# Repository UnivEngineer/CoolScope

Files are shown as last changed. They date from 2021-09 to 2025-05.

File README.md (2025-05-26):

# CoolScope
Telescope fan controller

CoolScope is a diy 2-channel fan controller based on Arduino Nano. It is used to cool down (thermostabilize) the 12 inch Meade LX200 telescope, but can be adapted to any other scope. It is assembled in a 3D printed case and mounted on the back on the scope. The device features 2 channels for 12V PWM fans, 4 temperature sensors DS18B20 (mounted on the scope's primary mirror, inside the scope's tube, inside device's case, and one external sensor connected via 3.5 mm jack), and 1602 LCD/OLED display to show stats and menu. The device is powered by 12V external power source, and draws up to 400 mA (depending on used fans).

The project consists of three parts:

Telescope_fans - Arduino sketch source code.
PCB - KiCad files of circuit schematics and PCB.
Case - SolidWorks and STL files of 3D model of the case.

The device can use any 80 mm 1602 LCD module with parallel interface (4 data lines). The best choice for astronomy accessory is a module with red symbols on a black background. Even better choice is a red Winstar 1602 OLED (WEH001602A), fully compatible electrically with LCD modules. OLED display performance is perfect at freezing temperatures, unlike STN LCD. The device supports both types of displays, there is a jumper on the PCB to tell the software which type of display module is connected.

The Arduino Nano can either be soldered to the main PCB through its PLS pins, or installed in a DIP socket, but you have to cut and solder pins directly to Nano, otherwise it may not fit under the display module.

The device has the circuit which protects it against wrong power polarity, and power voltage monitor, which can be used to control telescope's battery charge, and also used by software to auto-save settings to EEPROM memory on power loss.

----------------------------------------------------------------------------------

Short usage manual (v 1.5)

Device has 4 buttons: [menu], [<], [>], [ok].

Once powered up, you will see the info screen. It displays current temperatures reported by sensors, fans speed and duty, and power supply voltage. You may scroll through info screen modes by pressing [<] and [>] buttons. Legend:

- A - ambient temperature, i.e. sensor inside the device
- E - external temperature, i.e. external sensor connected via jack
- M - mirror temperature
- T - tube temperature (air inside the tube)
- [battery symbol] - power supply voltage
- [rotating fan symbol] - max of (front, rear) fans duty/RPM
- F - front fan duty/RPM
- R - rear fan duty/RPM

Pressing [menu] or [ok] button will bring up the settings. Press buttons [<] or [>] to scroll through options or increase/decrease values, [ok] to enter sub-level, [menu] to return back to upper level. The settings menu hierarchy is the following:

Settings
- Cooling
  - Fans enabled [values are "off", "on"]
  - Mode once cooled [values are "Keep delta T", "Keep blowing", "Keep drawing", "Stop"]
  - Target delta T [values are 0.05, 0.1, 0.2 ... 3.0 °C]
  - Cooling speed [values are 5, 10, 15 ... 100 %]
  - Keeping speed [values are 5, 10, 15 ... 100 %]
  - Pos. pressure [values are 0, 5, 10, 15 ... 100 %]
- Sensors
  - Target delta T pair [values are "Mirror and Ambient", "Mirror and External", "Mirror and Tube"]
  - Assign sensors [scroll through list of detected DS18B20 addresses and press [menu] to assign]
    - Mirror
    - Tube
    - Ambient
    - External
- Display
  - Brightness [values are 0, 1, ... 10]
  - Contrast [LCD only; values are 1, ... 10]
  - Timeout [values are "Disabled", 5, 10, 15, ..., 120 seconds]
  - Test [all pixels of display are filled until [menu] is pressed]
- Information
  - Uptime [uptime in days hours:minutes:seconds]
  - Fan stuck alarm [values are "off", "on"]
  - Low battery alarm [values are "off", "on"]
  - Battery alarm voltage [values are 8.0, 8.1, ... 12.0 volts]
  - Power voltage [current power supply voltage]
  - About

Pressing and holding the menu button, while on the info screen, will disable/enable cooling (the message "Fans enabled"/"Fans disabled" is displayed for a few seconds). This is a quicker way to stop fans than accessing "Cooling->Fans enabled" menu.

Depending on "Display->Timeout" settings, the display may turn off after a while (if LCD is used, only back-light will turn off). To turn on it back, simply press any button.

The device will run fans at "Cooling->Cooling speed" duty until specified delta T is reached. After that, it will either stop fans or keep them spinning at "Cooling->Keeping speed". Typically, you need the primary mirror of your scope to be in thermal equilibrium with outside air, so the "Target delta T pair" must be set to "Mirror and External", and external DS18B20 sensor plugged into the 3.5 mm jack. The "Ambient" sensor is mounted inside the device, thus may report higher temperatures because of observer breathing. For a balcony observations, the "Mirror and Tube" pair may give better results, because air at balcony is warmer than the outside air anyway.

To protect interior of the scope from the dust, intake fans must be covered with dust filters (HEPA is the best solution). Also it is important to keep the pressure inside the tube a bit higher than the atmosphere, otherwise unfiltered air with dust particles may be sucked in from holes and slits. Thus intake fans must spin somewhat faster that exhaust fans. The "Cooling->Pos. pressure" menu sets the percentage of the exhaust fans speed in relation to intake fans speed. Typical value is 30-50%. You can find it experimentally using a plastic bag capping the eyepiece slot of your scope: the bag must inflate.

V 1.2 - added auto switch to external sensor, then plugged in; added CRC check of data read from sensors.
V 1.3 - added support for graphical Winstar OLED (100x16 pixels) as a define, switch OLED/LCD is not supported in this case.
V 1.4 - fixed bug with "About" menu not working properly.
V 1.5 - added exhaust fans duty adjust.

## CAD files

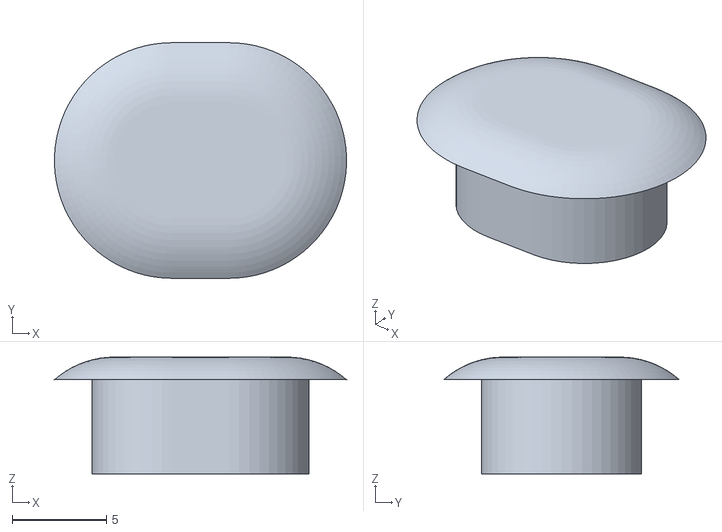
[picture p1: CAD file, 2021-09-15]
Сase/Dummy^Assembly.STL
15.5 x 12.5 x 6.20

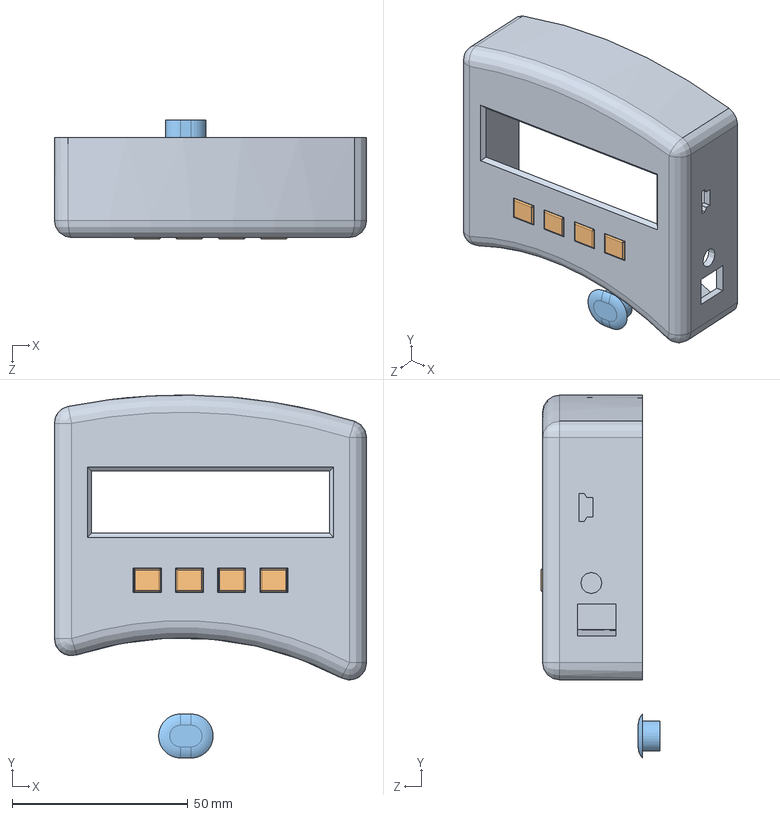
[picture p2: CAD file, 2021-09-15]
Сase/Assembly.SLDASM
88.8 x 103.2 x 33.8 mm
Case
Button1 x 4
Dummy^Assembly

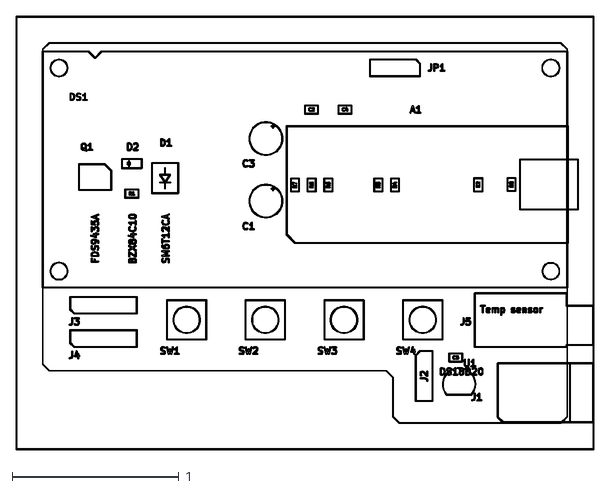
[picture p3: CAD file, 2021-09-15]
Сase/Telescope_fans-F_Fab.dxf
3.47 x 2.60

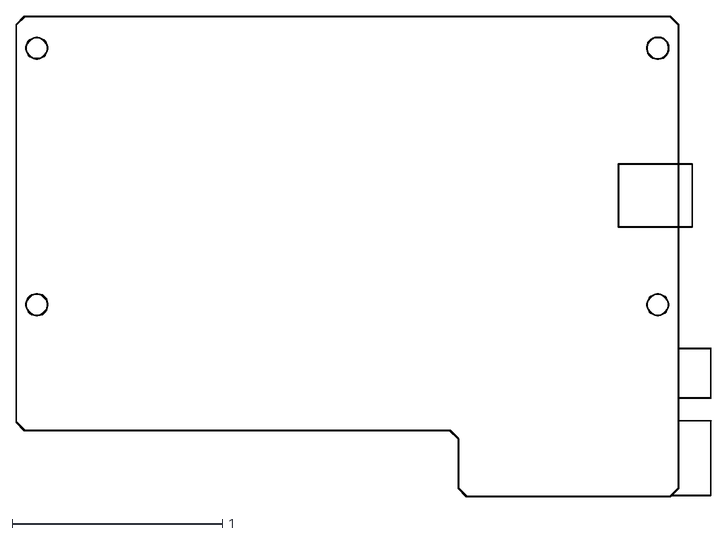
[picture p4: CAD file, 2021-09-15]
Сase/Telescope_fans-Edge_Cuts.dxf
3.30 x 2.29

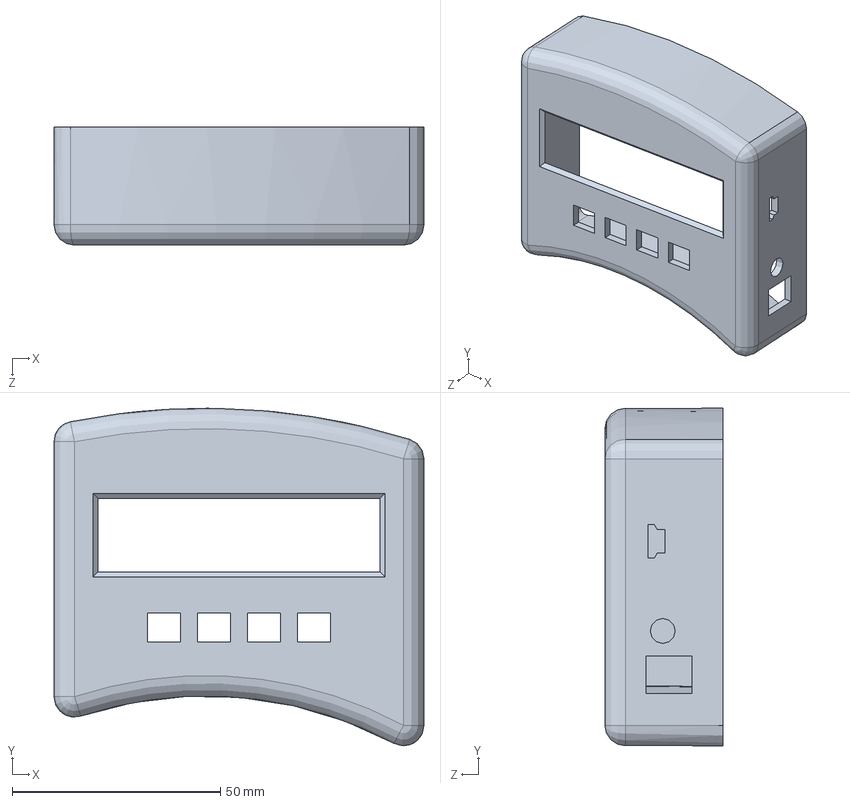
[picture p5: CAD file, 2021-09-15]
Сase/Case.SLDPRT
88.8 x 81.0 x 28.4 mm

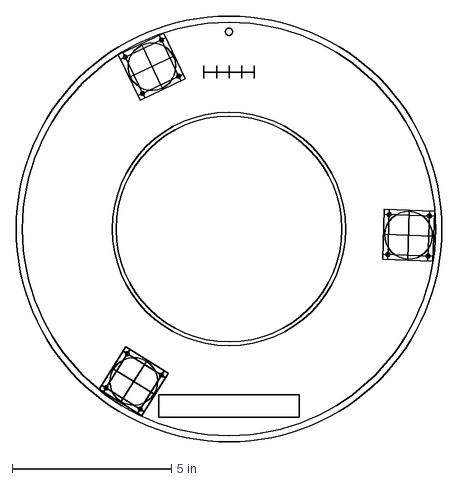
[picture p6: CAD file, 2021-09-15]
Сase/scope_back.dxf
13.4 x 13.4 in

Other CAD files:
Сase/Cover.SLDPRT
Сase/Button1.SLDPRT
Сase/Button1.STL
Сase/Case.STL
Сase/Cover.STL
Сase/Telescope_fans-B_Mask.dxf
Сase/Telescope_fans-F_SilkS.dxf

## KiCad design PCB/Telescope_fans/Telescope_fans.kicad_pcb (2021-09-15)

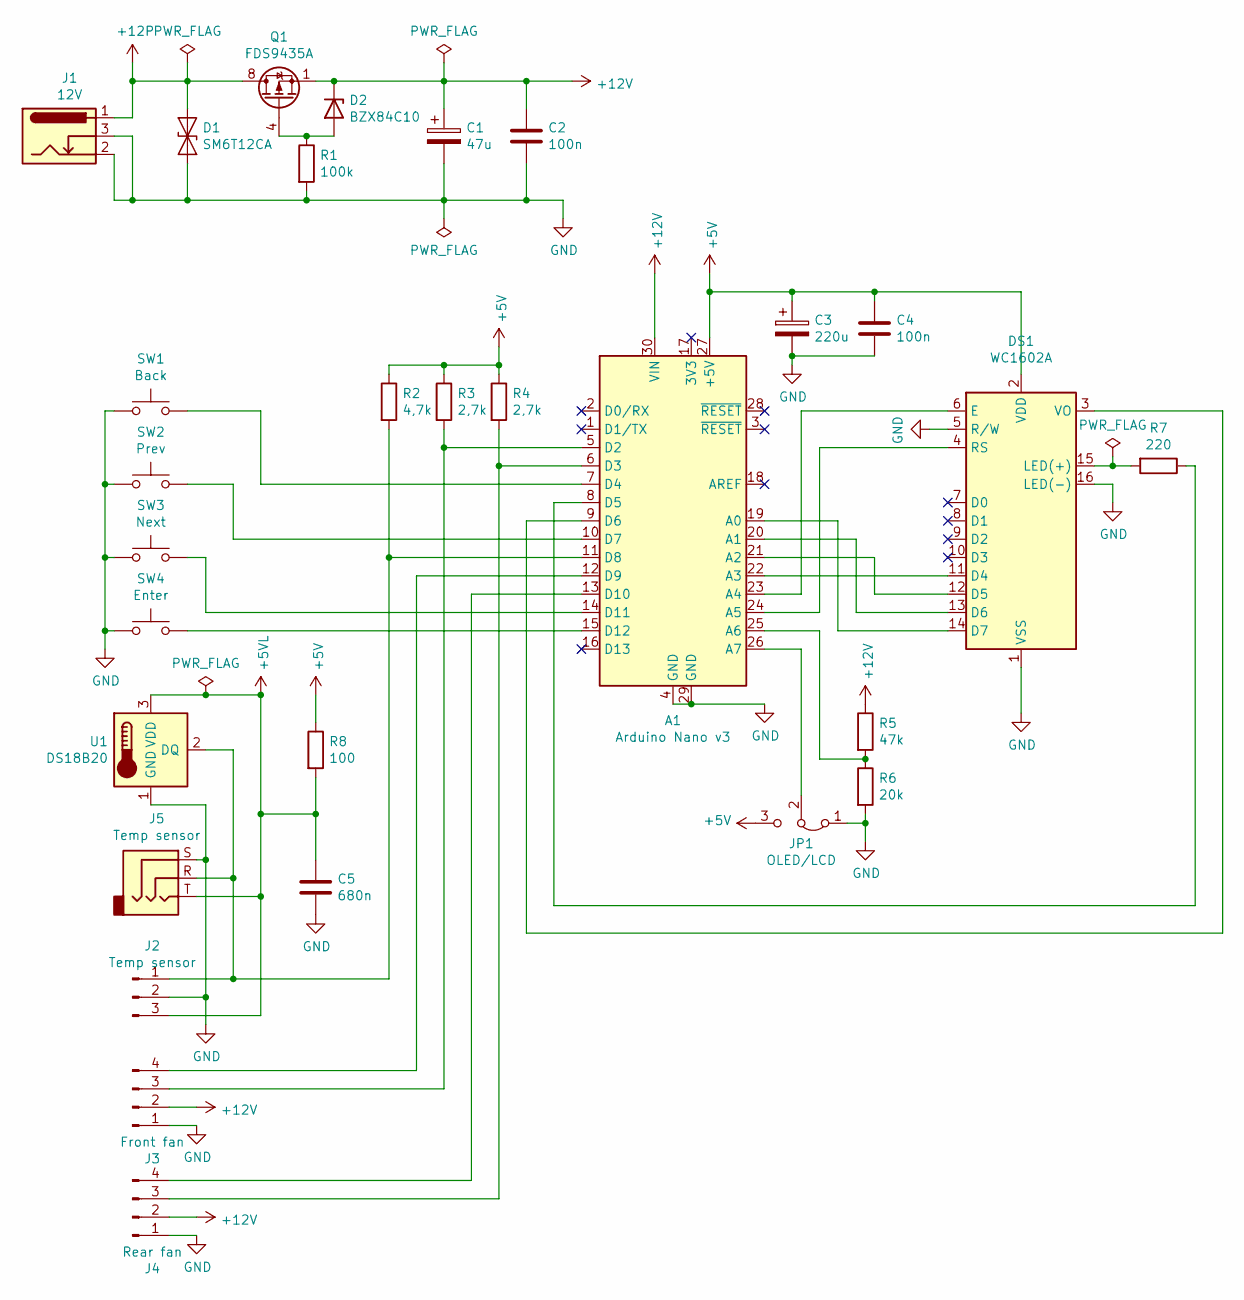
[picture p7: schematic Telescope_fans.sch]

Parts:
A1: Arduino Nano v3; Arduino_Nano_Chinese
C1: 47u; CP_Radial_D5.0mm_P2.50mm
C2, C4: 100n; C_0805_2012Metric_Pad1.18x1.45mm_HandSolder
C3: 220u; CP_Radial_D5.0mm_P2.50mm
C5: 680n; C_0805_2012Metric_Pad1.18x1.45mm_HandSolder
D1: SM6T12CA; D_SMB_Handsoldering
D2: BZX84C10; D_SOT-23_ANK
DS1: WC1602A
J1: 12V; BarrelJack_Horizontal
J2: Temp sensor; PinHeader_1x03_P2.54mm_Vertical
J3: Front fan; PinHeader_1x04_P2.54mm_Vertical
J4: Rear fan; PinHeader_1x04_P2.54mm_Vertical
J5: Temp sensor; Jack_3.5mm_CUI_SJ1-3533NG_Horizontal
JP1: OLED/LCD; PinHeader_1x03_P2.54mm_Vertical
Q1: FDS9435A; SOIC-8_3.9x4.9mm_P1.27mm
R1: 100k; R_0805_2012Metric_Pad1.20x1.40mm_HandSolder
R2: 4,7k; R_0805_2012Metric_Pad1.20x1.40mm_HandSolder
R3, R4: 2,7k; R_0805_2012Metric_Pad1.20x1.40mm_HandSolder
R5: 47k; R_0805_2012Metric_Pad1.20x1.40mm_HandSolder
R6: 20k; R_0805_2012Metric_Pad1.20x1.40mm_HandSolder
R7: 220; R_0805_2012Metric_Pad1.20x1.40mm_HandSolder
R8: 100; R_0805_2012Metric_Pad1.20x1.40mm_HandSolder
SW1: Back; SW_PUSH_6mm_H13mm
SW2: Prev; SW_PUSH_6mm_H13mm
SW3: Next; SW_PUSH_6mm_H13mm
SW4: Enter; SW_PUSH_6mm_H13mm
U1: DS18B20; TO-92L_Inline_Wide

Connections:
+5V: A1.27 (+5V), C3.1, C4.1, DS1.2 (VDD), JP1.3 (B), R2.1, R3.1, R4.1, R8.1
+5VL: C5.1, J2.3, J5.T, R8.2, U1.3 (VDD)
+12P: D1.1 (A1), J1.1, Q1.5 (D), Q1.6 (D), Q1.7 (D), Q1.8 (D)
+12V: A1.30 (VIN), C1.1, C2.1, D2.1 (K), J3.2, J4.2, Q1.1 (S), Q1.2 (S), Q1.3 (S), R5.1
GND: A1.4 (GND), A1.29 (GND), C1.2, C2.2, C3.2, C4.2, C5.2, D1.2 (A2), DS1.1 (VSS), DS1.5 (R/W), DS1.16 (LED(-)), J1.2, J1.3, J2.2, J3.1, J4.1, J5.S, JP1.1 (A), R1.2, R6.2, SW1.1, SW2.1, SW3.1, SW4.1, U1.1 (GND)
unnamed: A1.5 (D2), J3.3, R3.2
unnamed: A1.6 (D3), J4.3, R4.2
unnamed: A1.7 (D4), SW1.2
unnamed: A1.8 (D5), R7.1
unnamed: A1.9 (D6), DS1.3 (VO)
unnamed: A1.10 (D7), SW2.2
unnamed: A1.11 (D8), J2.1, J5.R, R2.2, U1.2 (DQ)
unnamed: A1.12 (D9), J3.4
unnamed: A1.13 (D10), J4.4
unnamed: A1.14 (D11), SW3.2
unnamed: A1.15 (D12), SW4.2
unnamed: A1.19 (A0), DS1.14 (D7)
unnamed: A1.20 (A1), DS1.13 (D6)
unnamed: A1.21 (A2), DS1.12 (D5)
unnamed: A1.22 (A3), DS1.11 (D4)
unnamed: A1.23 (A4), DS1.6 (E)
unnamed: A1.24 (A5), DS1.4 (RS)
unnamed: A1.25 (A6), R5.2, R6.1
unnamed: A1.26 (A7), JP1.2 (C)
unnamed: D2.2 (A), Q1.4 (G), R1.1
unnamed: DS1.15 (LED(+)), R7.2

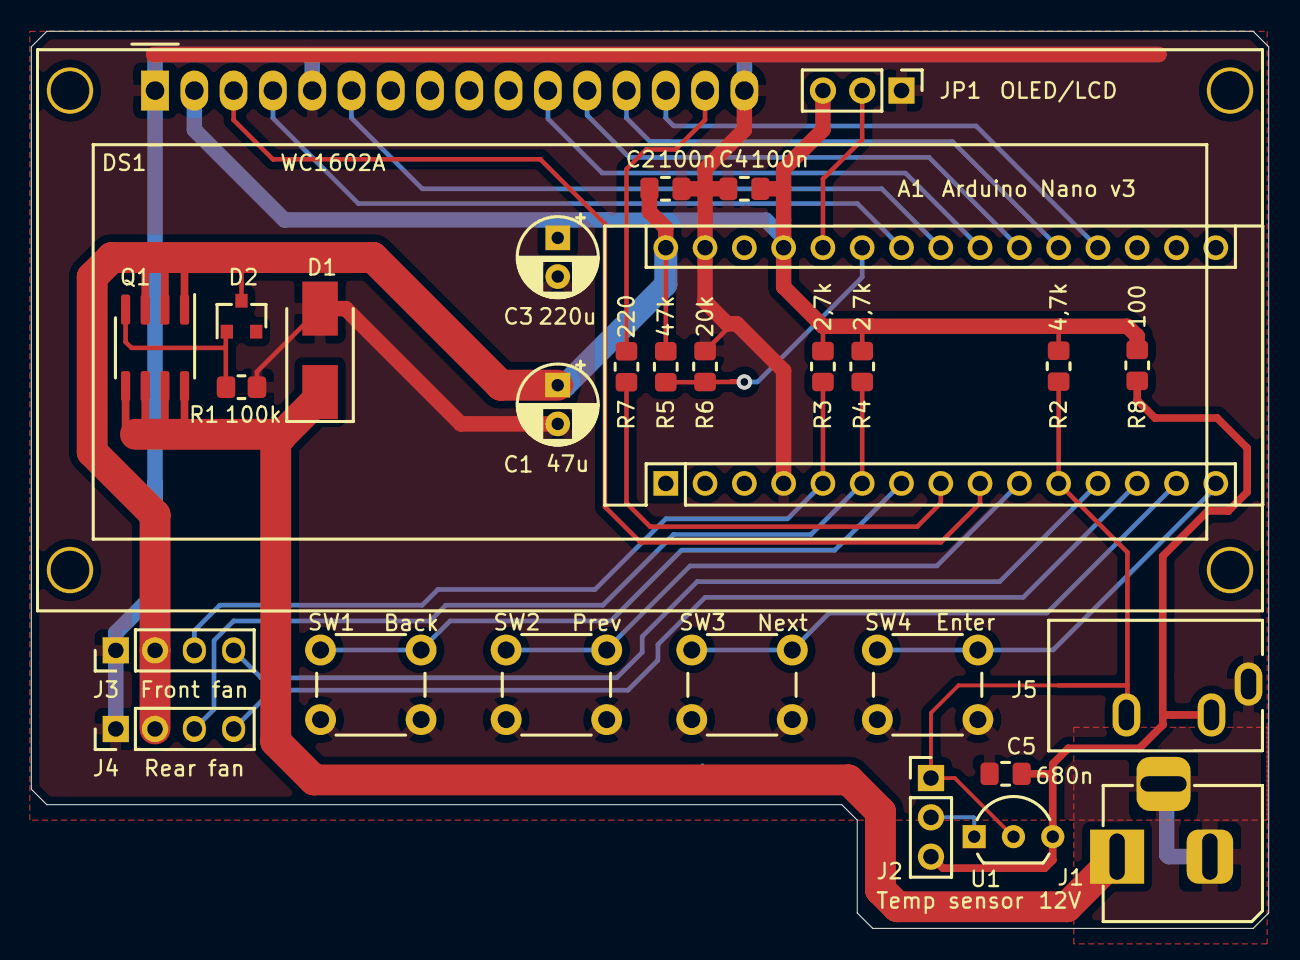
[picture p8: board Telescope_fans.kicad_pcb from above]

Board: 2 copper layers, 80.0 x 58.0 mm, 29 parts (0 on the bottom side), 26 nets.

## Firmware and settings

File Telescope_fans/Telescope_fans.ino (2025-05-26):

#define NANO
//------------------------------------------------------------------------------------------
#define VERSION "v 1.5"  // version string
//------------------------------------------------------------------------------------------
#define GRAPHICS_MODE // use graphics Winstar display
#define BI_LANG       // use second language, supported only in graphics mode
//#define DEBUG         // output debug info to Serial Monitor
//#define USE_DHT       // use DHT sensor
//------------------------------------------------------------------------------------------
#define LINE_LENGTH             16    // number of symbols in line
//------------------------------------------------------------------------------------------
// All times in milliseconds
#define POWER_DETECT_PERIOD     5     // period to measure power voltage and detect power loss
#define MAIN_LOOP_PERIOD        100   // main program loop peroid
#define TEMP_SENSOR_READ_PERIOD 1000  // period to read temperature from sensors
#define POWER_RESTORE_DELAY     500   // wait time before power restored signal
#define FAN_RPM_COUNT_TIME      1000  // period of fan RPM measurement (pulse accumulation)
#define FAN_STUCK_WAIT_TIME     2000  // report fan failure if it don't spin this long
#define FAN_STUCK_IGNORE_TIME   5000  // don't detect fan failure after cooling on/off
#define MSG_SHORT_TIME          100   // short message (blinking alerts) display time
#define MSG_LONG_TIME           2000  // long message ("fans enabled/disbled") display time
#define MSG_BLINK_HALFPERIOD    500   // half of message blinking period
#define EEPROM_WRITE_WAIT_TIME  10000 // delay between writes to EEPROM memory
#define OLED_SCREEN_SAVER       10000 // period of random shif of image on graphics Winstar OLED
//------------------------------------------------------------------------------------------



//------------------------------------------------------------------------------------------
// Used pins
//------------------------------------------------------------------------------------------
// Pin name (physical pin number on Arduino Nano board)
// Hardware interrupt pins: D2(5), D3(6)
// Hardware PWM pins:       D3(6), D5(8), D6(9), D9(12), D10(13), D11(14)
// Analog-read-only pins:   A6(20), A7(21)

#define DHT_PIN           8   // Digital pin connected to the DHT sensor
#define DS18B20_PIN       8   // Digital pin connected to the DS19B20 sensor(s)

#define TACH_1_PIN        2   // Pin for fan 1 tachometer - must be an interrupt capable pin (2 or 3 on Arduino Nano)
#define TACH_2_PIN        3   // Pin for fan 2 tachometer - must be an interrupt capable pin (2 or 3 on Arduino Nano)

#define PWM_1A_PIN        9   // Digital pin for PWM 1A channel
#define PWM_1B_PIN        10  // Digital pin for PWM 1B channel
#define PWM_2_PIN         3   // Digital pin for PWM 2  channel

#define PWM_BRIGHT_LCD    5   // Display brightness PWM
#define PWM_CONTRAST_LCD  6   // Display contrast   PWM

// Digital pins for 1602 disaply
#define LCD_D7_PIN        14  // A0(14)
#define LCD_D6_PIN        15  // A1(15)
#define LCD_D5_PIN        16  // A2(16)
#define LCD_D4_PIN        17  // A3(17)
#define LCD_E_PIN         18  // A4(18)
#define LCD_RS_PIN        19  // A5(19)

#define POWER_DETECT_PIN  A6  // A6(20) Power loss detection pin

#define LCD_DETECT_PIN    A7  // A7(21) Display type (LCD/OLED) jumper pin

#define BOARD_LED_PIN     13  // Onboard LED pin

// Digital pins for buttons
#define KEY_MENU_PIN      4
#define KEY_PREV_PIN      7
#define KEY_NEXT_PIN      11
#define KEY_ENTER_PIN     12
//------------------------------------------------------------------------------------------




//------------------------------------------------------------------------------------------
// Used modules
//------------------------------------------------------------------------------------------
#include "temp.h"
#include "vars.h"
#include "settings.h"
#include "state.h"
#include "fans.h"
#include "font.h"
#include "locale.h"
#include "display.h"
#include "keys.h"
#include "menu.h"
//------------------------------------------------------------------------------------------




//------------------------------------------------------------------------------------------
// Main code
//------------------------------------------------------------------------------------------

void setup()
{
#ifdef DEBUG
  Serial.begin(9600);
  Serial.println(F("Starting..."));
#endif

  settings.Init();
  fans.Init();
  display.Init();
  temp.Init();

#ifdef DEBUG
  Serial.println(F("Running..."));
#endif
}

//------------------------------------------------------------------------------------------

void loop()
{
  for (int i = 0; i < MAIN_LOOP_PERIOD / POWER_DETECT_PERIOD; ++i)
  {
    // Detect power loss and save settings to EEPROM
    if (settings.DetectPowerLoss())
    {
      // If power loss detected, first shot down main power consumers
      display.Off(true);
      fans.Off();

      // Then save data to EEPROM - we must have enough charge on the 12V capasitor
      settings.Save();
    }
    
    delay(POWER_DETECT_PERIOD);
  }

  settings.Update(MAIN_LOOP_PERIOD / POWER_DETECT_PERIOD);

  if (!settings.isPowerLost())
  {
    // Read keyboard
    keys.update();

    bool anyKey = keys.isClickedAny();
  
    if (display.isOff && (anyKey || fans.isStuck() || settings.isLowBattery() || settings.isPowerRestored()))
      display.On();
    else
    {
      if (anyKey)
        display.Touch();
  
      if (keys.Button[BT_MENU] .isHeld())  menu.onHold();

      if (keys.Button[BT_MENU] .isClick()) menu.onBack();
      if (keys.Button[BT_PREV] .isClick()) menu.onPrev();
      if (keys.Button[BT_NEXT] .isClick()) menu.onNext();
      if (keys.Button[BT_ENTER].isClick()) menu.onEnter();
    }
  
    // Read temperature sensors
    temp.Update();
  
    // Set fans speed and read fans RPM
    fans.Update();
  
    // Update disaply
    display.Update();
  }
}

//------------------------------------------------------------------------------------------

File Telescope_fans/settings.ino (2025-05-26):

//------------------------------------------------------------------------------------------
// Save/load settings to EEPROM, power loss detection
//------------------------------------------------------------------------------------------
CSettings settings;
//------------------------------------------------------------------------------------------
#define RESISTOR_TO_PWR     46.9f // 44.3f // power voltage measurement divider R1, kOhms
#define RESISTOR_TO_GND     20.1f // 17.9f // power voltage measurement divider R2, kOhms
#define ADC_TO_VOLTS        (5.0f / 1023.0f * (RESISTOR_TO_PWR + RESISTOR_TO_GND) / RESISTOR_TO_GND)
#define POWER_USB_VOLTS     5.0f  // power voltage considered as "powered by USB"
//------------------------------------------------------------------------------------------




//------------------------------------------------------------------------------------------
// Reads variables from EEPROM

void    CSettings::Init()
{
  pinMode(POWER_DETECT_PIN, INPUT);

#ifdef DEBUG
  Serial.println(F("Loading variables..."));
  char text2[128];
#endif

  int16_t v = 0;
  int  addr = 0;

  for (CVariable * var = CVariable::First; var != NULL; var = var->Next)
  {
    if (var->isValueAddress())
    {
      EEPROM.get(addr, var->address);
      addr += sizeof(var->address);

      #ifdef DEBUG
        sprintf(text, "addr = %i, EEPROM = ", addr);
        Serial.print(text);
        AddressToHexStr(var->address, text);
        Serial.println(text);
      #endif
    }
    else
    {
      EEPROM.get(addr, v);
      addr += sizeof(int16_t);
  
      // if value read from EEPROM is out of range, this is probably first run,
      // we must reset variable to default.
      if (!var->set(v))
        var->reset();
  
      #ifdef DEBUG
        sprintf(text2, "addr = %i, EEPROM = %i, var = %i", addr, v, var->value);
        Serial.println(text2);
      #endif
    }
  }
}

//------------------------------------------------------------------------------------------
// Writes variables to EEPROM

void    CSettings::Write()
{
#ifdef DEBUG
  Serial.println(F("Saving variables..."));
#endif

  int  addr = 0;

  for (CVariable * var = CVariable::First; var != NULL; var = var->Next)
  {
    if (var->isValueAddress())
    {
      EEPROM.put(addr, var->address);
      addr += sizeof(var->address);

      #ifdef DEBUG
        sprintf(text, "addr = %i, var = ", addr);
        Serial.print(text);
        AddressToHexStr(var->address, text);
        Serial.println(text);
      #endif
    }
    else
    {
      EEPROM.put(addr, var->value);
      addr += sizeof(var->value);
  
      #ifdef DEBUG
        sprintf(text, "addr = %i, var = %i", addr, var->value);
        Serial.println(text);
      #endif
    }
  }
}

//------------------------------------------------------------------------------------------
// Resets variables to defaults

void    CSettings::Reset()
{
#ifdef DEBUG
  Serial.println(F("Resetting variables..."));
#endif

  for (CVariable * var = CVariable::First; var != NULL; var = var->Next)
  {
    var->reset();

#ifdef DEBUG
    Serial.println(var->value);
#endif
  }
}

//------------------------------------------------------------------------------------------
// Writes variables to EEPROM if minimal time after last saving has passed

void    CSettings::Save()
{
  uint32_t t = millis();

  if (firstPowerLoss || (t - lastSaveTick > EEPROM_WRITE_WAIT_TIME))
  {
#ifdef DEBUG
      Serial.print(F("!!!! Power lost, saving variables !!!! V = "));
      Serial.println(voltage);
#endif
  
    Write();
    lastSaveTick = t;

    // Wait until last data chunck recorded to EEPROM
    delay(POWER_DETECT_PERIOD);

    // Indicate that data has been saved sucessfully with onboard LED
    digitalWrite(BOARD_LED_PIN, HIGH);
  }

  firstPowerLoss = false;
}

//------------------------------------------------------------------------------------------
// Returns true if power loss detected

bool    CSettings::DetectPowerLoss()
{
  // Measure 12V line voltage, convert to volts
  int v = analogRead(POWER_DETECT_PIN);
  voltage = (float)v * ADC_TO_VOLTS;

  voltageSum += voltage;

  // Detect power loss as a dropping of 12V line voltage.
  // Voltage threshold should be somewhat lower than the battery alarm setting.
  float powerLossVoltage = varBattAlarmVolt.getf() - 1.0f;
  powerLossVoltage = min(powerLossVoltage, 10.0f);

  // If voltage is < 5V, we are powering from USB, so don't
  // detect this as a power loss (USB debug mode).
  poweredByUSB = (voltage < POWER_USB_VOLTS);

  powerLostPrev = powerLost;
  powerLost = !poweredByUSB && (voltage < powerLossVoltage);

  // Delay before exit the power lost state
  uint32_t t = millis();
  if (powerLost)
    lastPowerLossTick = t;
  else if (t - lastPowerLossTick < POWER_RESTORE_DELAY)
    powerLost = true;

  return powerLost;
}

//------------------------------------------------------------------------------------------
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

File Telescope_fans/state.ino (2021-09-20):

//------------------------------------------------------------------------------------------
// State variables
//------------------------------------------------------------------------------------------
CState    state;
//------------------------------------------------------------------------------------------

CState::CState()
{
  for (int i=0; i<S_COUNT; ++i)
    temp[i] = NO_TEMP;
}

//------------------------------------------------------------------------------------------

bool  CState::isExtSensorAvailable()
{
  return state.temp[S_EXTERNAL] != NO_TEMP;
}

//------------------------------------------------------------------------------------------

bool  CState::isUseExtSensor()
{
  return isExtSensorAvailable() && (varDtSecondSensor.value != S_AMBIENT);
}

//------------------------------------------------------------------------------------------

void  CState::CalcTempDelta()
{
  int sensor = varDtSecondSensor.value;
  if ((sensor == S_EXTERNAL) && !isExtSensorAvailable())
    sensor = S_AMBIENT;

  if (temp[S_MIRROR] == NO_TEMP || temp[sensor] == NO_TEMP)
    tempDelta = NO_TEMP;
  else
    tempDelta = temp[S_MIRROR] - temp[sensor];
}

//------------------------------------------------------------------------------------------

const char * CState::GetFanSymbol(int duty)
{
  if (duty == 0)
      return FAN3;
  else
  {
    int animSpeed = display.isOLED ? 250 : 500;
    int phase = (millis() / animSpeed) % 3;
    switch (phase)
    {
      case 0:  return FAN1;
      case 1:  return FAN2;
      default: return FAN3;
    }
  }
}

//------------------------------------------------------------------------------------------

void  CState::PrintDeltaTHelper(int pos)
{
  char * buf = &text[pos];
  if (tempDelta == NO_TEMP)
    strcpy(buf, DELTA "T ---- ");
  else
  {
    if (fabs(tempDelta) < 10.0f)
      sprintf(buf, DELTA "T% 4.2f" DEG, tempDelta);
    else
      sprintf(buf, DELTA "T% 5.1f" DEG, tempDelta);
  }
}

//------------------------------------------------------------------------------------------

void  CState::PrintTempHelper(const char * symbol, int pos, float T)
{
  char * buf = &text[pos];
  if (T < -300.0f)
    sprintf(buf, "%s ---- ", symbol);
  else
    sprintf(buf, "%s% 5.1f" DEG, symbol, T);
}

//------------------------------------------------------------------------------------------

void  CState::PrintFanRPMHelper(const char * symbol, int pos, int duty, uint32_t RPM, bool fanSymbol)
{
  char * buf = &text[pos];
  sprintf(buf, "%s%s%5lu", symbol, fanSymbol ? GetFanSymbol(duty) : "", RPM);
}

//------------------------------------------------------------------------------------------

void  CState::PrintFanDutyHelper(const char * symbol, int pos, int duty, bool fanSymbol)
{
  char * buf = &text[pos];
  if (duty == 0)
    sprintf(buf, "%s%s off ", symbol, fanSymbol ? GetFanSymbol(duty) : "");
  else
    sprintf(buf, "%s%s% 4i%%", symbol, fanSymbol ? GetFanSymbol(duty) : "", duty);
}

//------------------------------------------------------------------------------------------

void  CState::PrintVoltHelper(const char * symbol, int pos)
{
  char * buf = &text[pos];
  if (settings.isPoweredByUSB())
    sprintf(buf, "%s [USB] ", symbol);
  else
    sprintf(buf, "%s% 5.1fV", symbol, settings.GetVoltage());
}

//------------------------------------------------------------------------------------------

char * CState::GetTempStr0()
{
  if (isUseExtSensor())
    PrintTempHelper(" E", 0, temp[S_EXTERNAL]);
  else
    PrintTempHelper(" A", 0, temp[S_AMBIENT]);

  PrintTempHelper(" M", 8, temp[S_MIRROR]);
  return text;
}

//------------------------------------------------------------------------------------------

char * CState::GetTempStr1()
{
  PrintDeltaTHelper(0);
  PrintTempHelper(" T", 8, temp[S_TUBE]);
  return text;
}

//------------------------------------------------------------------------------------------

char * CState::GetComboStr0()
{
  if (isUseExtSensor())
    PrintTempHelper(" E", 0, temp[S_EXTERNAL]);
  else
    PrintTempHelper(" A", 0, temp[S_AMBIENT]);

  PrintVoltHelper(" " BATT, 8);
  
  return text;
}

//------------------------------------------------------------------------------------------

char * CState::GetComboStr1Style1()
{
  PrintDeltaTHelper(0);
  PrintFanDutyHelper(" ", 8, max(fanDuty1, fanDuty2), true);
  return text;
}

//------------------------------------------------------------------------------------------

char * CState::GetComboStr1Style2()
{
  PrintDeltaTHelper(0);
  PrintFanRPMHelper(" ", 8, max(fanDuty1, fanDuty2), max(fanRPM1, fanRPM2), true);
  return text;
}

//------------------------------------------------------------------------------------------

char * CState::GetTempFansStr0Style1()
{
  if (isUseExtSensor())
    PrintTempHelper(" E", 0, temp[S_EXTERNAL]);
  else
    PrintTempHelper(" A", 0, temp[S_AMBIENT]);

  PrintFanDutyHelper(" F", 8, fanDuty1, true);
  return text;
}

//------------------------------------------------------------------------------------------

char * CState::GetTempFansStr1Style1()
{
  PrintDeltaTHelper(0);
  PrintFanDutyHelper(" R", 8, fanDuty2, true);
  return text;
}

//------------------------------------------------------------------------------------------

char * CState::GetTempFansStr0Style2()
{
  if (isUseExtSensor())
    PrintTempHelper(" E", 0, temp[S_EXTERNAL]);
  else
    PrintTempHelper(" A", 0, temp[S_AMBIENT]);

  PrintFanRPMHelper(" F", 8, fanDuty1, fanRPM1, true);
  return text;
}

//------------------------------------------------------------------------------------------

char * CState::GetTempFansStr1Style2()
{
  PrintDeltaTHelper(0);
  PrintFanRPMHelper(" R", 8, fanDuty2, fanRPM2, true);
  return text;
}

//------------------------------------------------------------------------------------------

char * CState::GetFansStr0()
{
  PrintFanDutyHelper("Front", 0, fanDuty1,          false);
  PrintFanRPMHelper (" ",    10, fanDuty1, fanRPM1, false);
  return text;
}

//------------------------------------------------------------------------------------------

char * CState::GetFansStr1()
{
  PrintFanDutyHelper(" Rear", 0, fanDuty2,          false);
  PrintFanRPMHelper (" ",    10, fanDuty2, fanRPM2, false);
  return text;
}

//------------------------------------------------------------------------------------------

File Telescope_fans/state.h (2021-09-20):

#ifndef STATE_H
#define STATE_H
//------------------------------------------------------------------------------------------
// State variables
//------------------------------------------------------------------------------------------

class   CState
{
public:

  float temp[S_COUNT];
  float tempDelta = 0.0f;

#ifdef USE_DHT
  float tempBoard = 0.0f;
  float humidity  = 0.0f;
#endif

  uint32_t fanRPM1 = 0;
  uint32_t fanRPM2 = 0;

  uint8_t  fanDuty1 = 0; // in %
  uint8_t  fanDuty2 = 0; // in %

  CState();

  void  CalcTempDelta();

  char * GetTempStr0();
  char * GetTempStr1();
  char * GetComboStr0();
  char * GetComboStr1Style1();
  char * GetComboStr1Style2();
  char * GetTempFansStr0Style1();
  char * GetTempFansStr1Style1();
  char * GetTempFansStr0Style2();
  char * GetTempFansStr1Style2();
  char * GetFansStr0();
  char * GetFansStr1();

private:

  bool  isExtSensorAvailable();
  bool  isUseExtSensor();

  const char* GetFanSymbol(int duty);
  void  PrintDeltaTHelper (int pos);
  void  PrintTempHelper   (const char * symbol, int pos, float T);
  void  PrintFanRPMHelper (const char * symbol, int pos, int duty, uint32_t RPM,  bool fanSymbol);
  void  PrintFanDutyHelper(const char * symbol, int pos, int duty,                bool fanSymbol);
  void  PrintVoltHelper   (const char * symbol, int pos);
};

//------------------------------------------------------------------------------------------
extern  CState  state;
//------------------------------------------------------------------------------------------
#endif // STATE_H

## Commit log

2021-09-15 Arduino sketch
    "Firmware" for the CoolScope fan controller. Will be updated.
2021-09-15 PCB project for KiCad
    Schematics and PCB project for KiCad
    [Telescope_fans.kicad_pcb, Telescope_fans.sch]
2021-09-15 Case drawing project for SolidWorks
    Case, buttons and hole dummy project for SolidWorks. Includes STL files for 3D printing, and dxf files exported from the PCB project to use as a sketch.
    [Assembly.SLDASM, Button1.SLDPRT, Button1.STL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]
2024-05-31 Fixed info/about in Russian mode
    [Telescope_fans.ino, keys.ino, locale.ino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]
2025-05-26 V1.5
    - Added exhaust fans percentage settings
    - fixed typos in readme
    [Telescope_fans.ino, fans.ino, menu.ino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]
